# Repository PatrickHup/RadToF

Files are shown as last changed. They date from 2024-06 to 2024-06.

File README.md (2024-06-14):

<!--
*** Template source: https://github.com/othneildrew/Best-README-Template/blob/master/README.md
-->

<!-- PROJECT SHIELDS -->
<!--
*** I'm using markdown "reference style" links for readability.
*** Reference links are enclosed in brackets [ ] instead of parentheses ( ).
*** See the bottom of this document for the declaration of the reference variables
*** for contributors-url, forks-url, etc. This is an optional, concise syntax you may use.
*** https://www.markdownguide.org/basic-syntax/#reference-style-links
-->

<!-- PROJECT LOGO -->
<br />
<p align="center">
  <a>
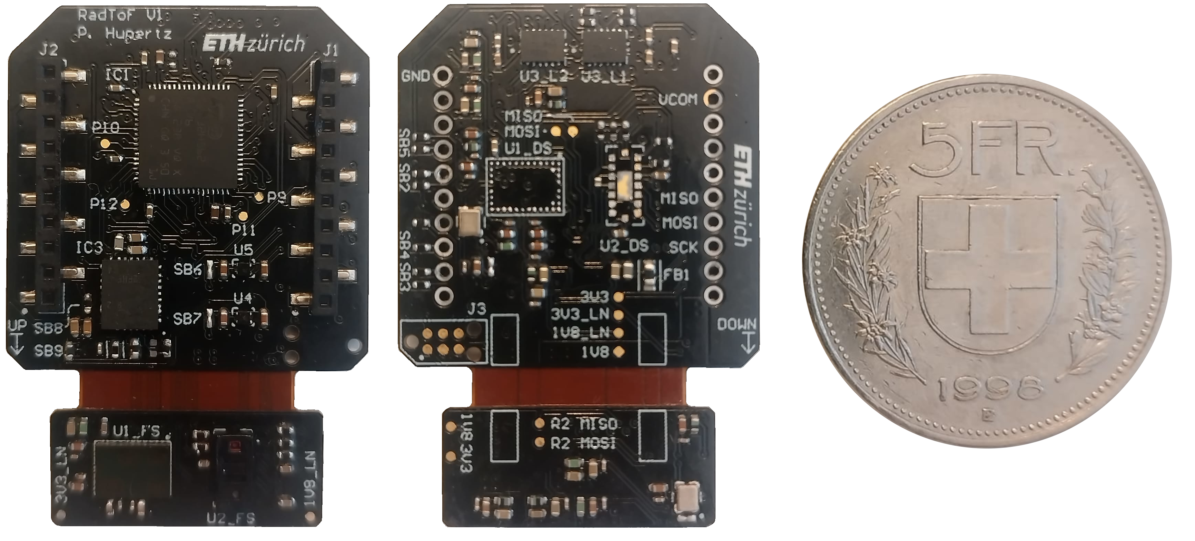
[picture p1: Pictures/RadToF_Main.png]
    
  </a>

  <h3 align="center">"RadToF" Radar/ToF Deck</h3>

  <p align="center">
    60 GHz radar extension board for the CrazyFlie 2.1
    <br />
    <a href="https://github.com/PatrickHup/Test"><strong>Explore the docs »</strong></a>
  </p>
</p>

<!-- TABLE OF CONTENTS -->
## Table of Contents

* [About the Project](#about-the-project)
* [Hardware](#hardware)
  * [Components](#hardware)
  * [PCB](#pcb)
* [Firmware](#firmware)
  * [Getting started](#getting-started)
* [Related work](#related-work)
* [Acknowledgment](#acknowledgment)

<!-- ABOUT THE PROJECT -->
## About The Project

The RadToF project aims to develop a Printed Circuit Board (PCB) optimized for drones, with a key focus on implementing the 60 GHz radar by Infineon Technologies. The goal is to enable drones to navigate more effectively and efficiently, driven by the increasing importance of autonomous nano drones across various sectors where sophisticated perception systems are crucial for safety and operational efficiency. By equipping drones with a radar system that delivers precise and reliable data, collision risks can be minimized, and operational autonomy can be improved.

**WARNING: USE AT YOUR OWN RISK, THERE MAY BE BUGS IN BOTH SOFTWARE AND HARDWARE**

## Hardware

The PCB accommodates four sensors: a radar and a depth camera pointing forwards, and the same setup pointing downwards. This board also includes an MCU that processes data before sending it to the CrazyFlie. The final board measures 3 cm x 4 cm and weighs 3.15 g.

### Components
The main sensor is the 60 GHz radar by Infineon Technologies, using FMCW (Frequency Modulated Continuous Wave) operations to measure distances. The radar features a compact design with a built-in transmitter and three receivers. Additionally, we utilize an 8x8 zone ranging sensor by STMicroelectronics. The MCU chosen for this project is the STM32H562RIV6, selected for its performance and small form factor.

An important aspect of the board is its power supply. The radar requires ultra-low noise 1V8 and 3V3, achieved using the "Ultra low-noise low ripple" power supply by Texas Instruments.

Main components:

* [BGT60TR13C][BGT60TR13C_url],			  60 GHz radar
* [VL53L8CX][VL53L8CX_url],     		  ToF multizone ranging sensor
* [STM32H562RIV6][STM32H562RIV6_url],		  Microcontroller
* [TPSM82912RDUR][TPSM82912RDUR_url],		  Ultra low noise switching regulator

Additional components:

* [TPS7A2018PDQNR][TPS7A2018PDQNR_url], 	  Ultra low noise LDO
* [SN74AXC4T774BQB][SN74AXC4T774BQB_url],	  Level shifter

### PCB 
The RadToF printed circuit board (PCB) is fabricated on a 4-layer Flex-Rigid PCB with a rigid PCB thickness of 0.84mm and a flex thickness of 0.16mm. Further information about the PCB can be found here:

File                                  | Content
--------------------------------------|--------
[RadToF.pdf]                          | Schematics of the deck.  
[RadToF_PDF3D.pdf]                    | Layout 3D view with details of components and nets.
[RadToF_BOM.xlsx]		      | Bill of material for the Deck PCB.
[RadToF_Draftsman.pdf]   	      | Draftsman of the PCB.
[RadToF.xls]		              | Layer stack of the Flex PCB.

The Altium project file [RadToF.prjpch] can be opened and edited using Altium Designer version 24.3.1

Top and bottom view of the board:

<p align="center">
	<a>
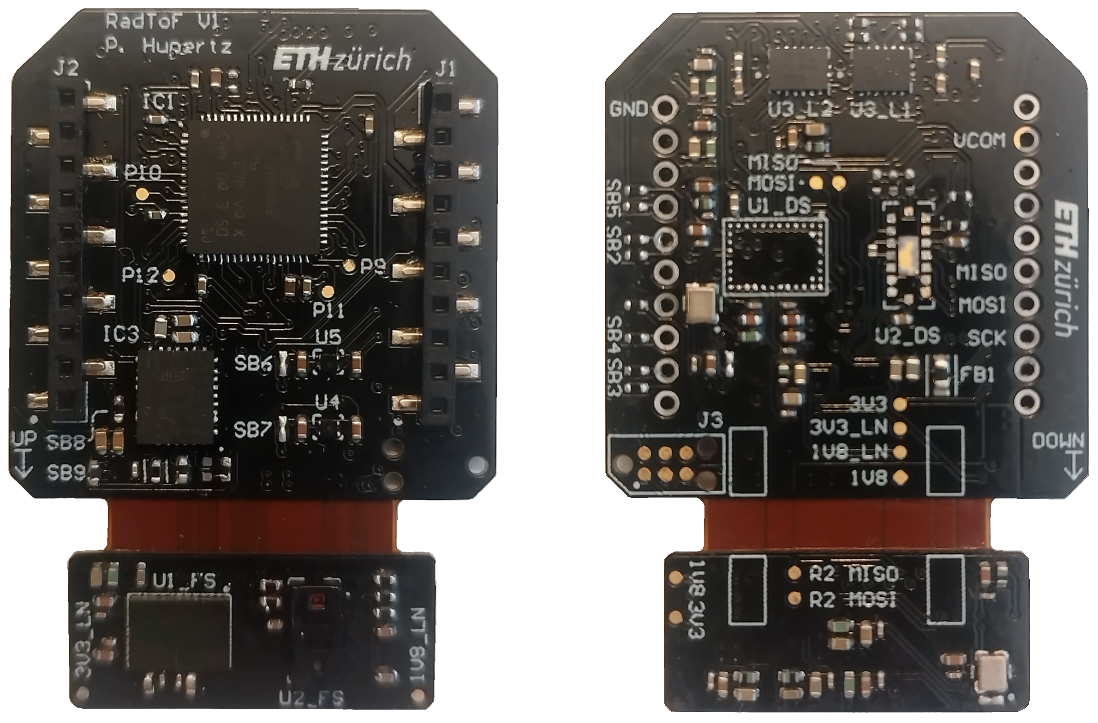
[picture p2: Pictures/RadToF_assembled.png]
	    
	</a>
</p>

#### Solder instruction:

#### Top side:

1. Pre-heat the PCB over 2-3 hours from room temperature to 250 °C to allow water molecules in the flex PCB to evaporate. This prevents delamination.
2. Apply 217 °C solder paste on the side marked "Top" with the help of a stencil if available. NOTE: do not apply solder paste on sensor pads.
3. Place components. Except for the sensors (radar and ToF).
5. Place the assembled board, "Top" side up, on pre preheated (250 °C) hot plate.
6. Wait for the solder paste to melt and remove to cool.
7. Verify the functionality of the power supply by checking voltages on debug pads.

#### Bottom side:

1. Apply 217 °C solder paste on the side marked "Bottom" with the help of a stencil if available. NOTE: do not apply solder paste on sensor pads.
2. Place components. Except for the sensors (radar and ToF).
3. Place the assembled board, "Bottom" side up, on pre preheated (150 °C) hot plate.
4. Use a hot air gun, set to 395 °C, to carefully melt the solder paste.
5. Verify the functionality of the MCU by trying to program it.

#### Radar soldering:

1. Do not apply solder paste
2. Place on 150 °C pre-heated hot plate
3. Heat with a heat gun set to 395 °C untill soldered

NOTE: if radar soldered unevenly, remove solder paste on pads and radar then re-ball radar with stencil

#### ToF sensor soldering:

WARNING: high temperature might damage ToF sensors plastic housing

1. Apply 138 °C solder paste on pads
2. Place on pre-heated hot plate at 150 °C
3. Carefully apply heat with a hot air gun

## Firmware

Needed software:

* [STM32cubeIDE][stm32cubeide_url], 		STM32 programmer and compiler version 1.15.1

The current state of the firmware is to be able to verify if the board is functional or not. The driver of the radar was provided by Tim Distel and the driver of the ToF can be found here: [ToF driver][ToF_driver_url].

### Getting started:

#### Material:

1. CrazyFlie 2.1
2. RadToF expansion deck
3. laptop
4. ST-LINK

#### How to program extension board:

1. Download STM32cubeIDE and the [Firmware] folder
2. open [.project] file with STM32cubeIDE (version 1.15.1)
3. Connect the extension board with a computer with ST-LINK
4. Compilie and upload firmware

## Related work

If you are interested in this work, you might also be interested in these:

1. [ToF deck][ToF_deck_url] offers a different approach for the extension board, featuring a ToF sensor facing forwards and backward.
2. [Quad deck][quad_deck_url] offers four ToF sensors, facing in every direction.
3. [Flow deck V2][flow_deck_url] offers a ToF and optical flow sensor facing downwards.

## Acknowledgment

Thanks go to:

Professor: Prof. Dr. Luca Benini

Supervisors: Dr. Tomasso Polonelli and Andrea Ronco

PCB experts: Hanna Müller and Alfonso Blanco

Additional help: Tim Distel and Luka Schultess

<!-- MARKDOWN LINKS & IMAGES -->
<!-- https://www.markdownguide.org/basic-syntax/#reference-style-links -->

<!--Subsection Hardware-->
[VL53L8CX_url]:    			https://www.st.com/resource/en/datasheet/vl53l8cx.pdf
[crazyflie_url]:   			https://www.bitcraze.io/products/crazyflie-2-1/
[BGT60TR13C_url]:			https://www.infineon.com/dgdl/Infineon-DS_BGT60TR13C-DataSheet-v02_49-EN.pdf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
[STM32H562RIV6_url]:			https://www.st.com/resource/en/datasheet/stm32h562ag.pdf
[TPSM82912RDUR_url]:			https://www.ti.com/lit/ds/symlink/tpsm82913e.pdf
[TPS7A2018PDQNR_url]:			https://www.ti.com/lit/ds/symlink/tps7a20.pdf
[SN74AXC4T774BQB_url]:			https://www.ti.com/lit/ds/symlink/sn74axc4t774.pdf
[stm32cubeide_url]: 			https://www.st.com/en/development-tools/stm32cubeide.html

[ToF_driver_url]: 			https://www.st.com/en/embedded-software/stsw-img040.html
[ToF_deck_url]: 			https://github.com/ETH-PBL/Matrix_ToF_Drones
[quad_deck_url]:			https://github.com/ETH-PBL/NanoSLAM
[flow_deck_url]:			https://www.bitcraze.io/products/flow-deck-v2/
<!--Subsection PCB-->
[RadToF.pdf]:                          /Hardware/Project_Output/RadToF.pdf
[RadToF_PDF3D.pdf]:                    /Hardware/Project_Output/RadToF_PDF3D.pdf
[RadToF_BOM.xlsx]:                     /Hardware/Project_Output/RadToF_BOM.xlsx
[RadToF_Draftsman.pdf]:                /Hardware/Project_Output/RadToF_Draftsman.pdf
[RadToF.xls]:                          /Hardware/Project_Output/RadToF.xls
[RadToF.prjpch]:                       /Hardware/RadToF.PrjPcb
[.project]:			       /Firmware/.project
[Firmware]:			       /Firmware

[stmcubeIDE_url]:	               https://www.st.com/en/development-tools/stm32cubeide.html
[altium_url]:	                       https://www.altium.com/

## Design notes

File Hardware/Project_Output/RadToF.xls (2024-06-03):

Board Stack Report
Stack Up |  |  | Layer Stack
Layer | Full stack | Flex stack | Name | Material | Thickness | Constant
1 |  |  | Top Overlay |  | 0mil
2 |  |  | Flex stack Top Coverlay | FC-001 | 1.476mil | 4
3 |  |  | Top Solder | Solder Resist | 0.8mil | 3.5
4 |  |  | Top Layer |  | 1.4mil
5 |  |  | Dielectric 4 | FR4 HTG | 9.8mil | 4.1
6 |  |  | Dielectric 2 | 1080 | 2.8mil | 4.1
7 |  |  | Layer 1 | CF-004 | 0.7mil
8 |  |  | Dielectric 1 | Polyimide | 2mil | 4.8
9 |  |  | Layer 2 | CF-004 | 0.7mil
10 |  |  | Dielectric 5 | 1080 | 2.8mil | 4.1
11 |  |  | Dielectric 3 | FR4 HTG | 9.8mil | 4.1
12 |  |  | Bottom Layer |  | 1.4mil
13 |  |  | Bottom Solder | Solder Resist | 0.8mil | 3.5
14 |  |  | Flex stack Bottom Coverlay | FC-001 | 1.476mil | 4
15 |  |  | Bottom Overlay |  | 0mil
 | Height : 33mil | Height : 6.353mil

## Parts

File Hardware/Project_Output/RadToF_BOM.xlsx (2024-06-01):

Line # | Name | Description | Designator | Revision ID | Revision State | Revision Status | Quantity | Manufacturer 1 | Manufacturer Part Number 1 | Manufacturer Lifecycle 1 | Supplier 1 | Supplier Part Number 1 | Supplier Unit Price 1 | Supplier Subtotal 1
 | Capacitor 100nF +/-20% 50V 0402 | Chip Capacitor, 100nF +/-20%, 50V, 0402, Thickness 0.6 mm | C1_DS, C1_FS, C2_DS, C2_FS, C14, C16_DS, C16_FS, C31, C33, C34, C35, C37, C38, C39, C40, C41, C42 |  | Unknown server |  | 17 | Murata | GRM155R71H104KE14D | Volume Production | Mouser | 81-GRM155R71H104KE4D | 0.01371 | 0.23314
 | C_GRM035R60J475ME15D | CAP CER 4.7uF 6.3V X5R 0201 | C5_DS, C5_FS |  | Unknown server |  | 2 | Murata | GRM035R60J475ME15D | Volume Production | Digikey | 490-13230-1-ND | 0.21943 | 0.43885
 | C_GRM155R61A106ME11D | CAP CER 10uF 10V X5R 20% 0402 | C6_DS, C6_FS, C9_DS, C9_FS, C10_DS, C10_FS, C17_DS, C17_FS, C19_DS, C19_FS, C52, C53 |  | Unknown server |  | 12 | Murata | GRM155R71H103KA88D | Volume Production | Mouser | 81-GRM155R71H103KA8D | 0.01189 | 0.14263
 | C_GRM155R61E105KA12J | CAP CER 1uF 25V X5R 0402 | C7_DS, C7_FS, C12_DS, C12_FS, C20_DS, C20_FS, C22_DS, C22_FS, C24_DS, C24_FS, C26_DS, C26_FS, C28_DS, C28_FS, C42_OSC_D, C42_OSC_F, C56, C57, C58, C59 |  | Unknown server |  | 20 | Murata | GRM155R61E105KA12J | Volume Production | Farnell | 3790417 | 0.01419 | 0.28388
 | C_GRM033R70J103JA01D | CAP CER 10nF 6.3V X7R 0201 | C8_DS, C8_FS, C11_DS, C11_FS, C13_DS, C13_FS, C18_DS, C18_FS, C21_DS, C21_FS, C23_DS, C23_FS, C25_DS, C25_FS, C27_DS, C27_FS, C29_DS, C29_FS, C43_OSC_D, C43_OSC_F |  | Unknown server |  | 20 | Murata | GRM033R70J103JA01D | Volume Production | Mouser | 81-GRM033R70J103JA1D | 0.00823 | 0.16457
 | Capacitor 2,2µF +/-20% 10V 0402 | Chip Capacitor, 2,2µF +/-20%, 10V, 0402, Thickness 0.6 mm | C15, C32 |  | Unknown server |  | 2 | Murata | GRM155R61C225KE11D | Volume Production | Arrow Electronics | GRM155R61C225KE11D | 0.14208 | 0.28416
 | C_GRM155R71H152JA01D | CAP CER 1.5nF 50V X7R 0402 | C30_DS, C30_FS |  | Unknown server |  | 2 | Murata | GRM155R71H103KA88D | Volume Production | Mouser | 81-GRM155R71H103KA8D | 0.01189 | 0.11886
 | C_GRM158R60J226ME01D | CAP CER 22uF 6.3V X5R 0402 | C47, C48, C49, C50, C51 |  | Unknown server |  | 5 | Murata | GRM155R71H103KA88D | Volume Production | Mouser | 81-GRM155R71H103KA8D | 0.01189 | 0.11886
 | C_GRT033C80J224KE01D | CAP CER 0.22uF 6.3V X6S 0201 | C55 |  | Unknown server |  | 1 | Murata | GRT033C80J224KE01D | Volume Production | Arrow Electronics | GRT033C80J224KE01D | 0.0832 | 0.0832
 | BLE18PS080SN1D | Ferrite Chip Bead 8A 8.5Ohm 2-Pin 0603 Paper T/R | FB1 |  | Unknown server |  | 1 | Murata | BLE18PS080SN1D | Volume Production | Digikey | 490-BLE18PS080SN1DCT-ND | 0.256 | 0.256
 | STM32H562RIV6 | ARM Microcontrollers - MCU Arm Cortex-M33 32-bit 250 MHz, up to 2 Mbytes of Flash, 640KB of RAM, I3C, DCMI | IC1 |  | Not managed |  | 1
 | TPSM82912RDUR | Switching Voltage Regulators 17-V, 2-A low-noise and low-ripple buck module with integrated ferrite bead filter compensation 28-B0QFN -40 to 125 | IC3 |  | Not managed |  | 1
 | Left | Header to connect to crazy flie pins | J1 |  | Not managed |  | 1
 | Right | Header to connect to crazy flie pins | J2 |  | Not managed |  | 1
 | TC2030-MCP-NL | CABLE TAG-CONNECT IN-CIRCUIT | J3 |  | Not managed |  | 1
 | L_LQG15WZ4N7B02D | IND 4.7nH 800mA 110 mOHM 0402 | L1_DS, L1_FS, L2_DS, L2_FS, L3_DS, L3_FS, L4_DS, L4_FS, L5_DS, L5_FS, L6_DS, L6_FS |  | Unknown server |  | 12 | Murata | LQG15WZ4N7B02D | Volume Production | Mouser | 81-LQG15WZ4N7B02D | 0.13988 | 1.68
 | Test Pad |  | P1_DS, P1_FS, P2_DS, P2_FS, P3_DS, P3_FS, P4_DS, P4_FS |  | Not managed |  | 8
 |  |  | P5, P6, P7, P8, P9, P10, P11, P12 |  | Not managed |  | 8
 | Resistor 47K5 +/-1 % 0402 63 mW | Chip Resistor, 47,5 kOhms, +/-1 %, 63 mW, -55 to 155 degC, 0402 | R1_DS, R1_FS, R2_DS, R2_FS, R3_DS, R3_FS, R4_DS, R4_FS, R5_DS, R5_FS, R6 |  | Unknown server |  | 11 | Vishay | CRCW040247K5FKED | Volume Production | Newark | 52K7100 | 0.00457 | 0.05029
 | Resistor 10K +/-1 % 0402 63 mW | Chip Resistor, 10 kOhms, +/-1 %, 63 mW, -55 to 125 degC, 0402 | R7 |  | Unknown server |  | 1 | Panasonic | ERJ-2RKF1002X | Volume Production | Digikey | P10.0KLCT-ND | 0.09143 | 0.09143
 | 301KR2F | 301K 0.063W 1% 0402 (1005 Metric) SMD | R8, R9, R10, R13, R17, R18, R23, R24 |  | Unknown server |  | 8
 | 4.87k | Automotive Metal Thin Film Chip Resistor, 0402, 4.87kΩ, 0.1%, 25ppm/°C, 0.0625W, 75V | R11 |  | Unknown server |  | 1 | Susumu | RG1005P-4871-B-T5 | Volume Production | Mouser | 754-RG1005P-4871-BT5 | 0.24685 | 0.24685
 | Resistor 15k +/-1% 0402 63 mW | Chip Resistor, 15 KOhm, +/- 1%, 0.063 W, -55 to 155 degC, 0402 (1005 Metric) | R12 |  | Unknown server |  | 1 | Yageo | RC0402FR-0715KL | Volume Production | Rs | 6186009 | 0.00177 | 0.00177
 | Jumper 0402 | Jumper 0402 | R14, R15 |  | Unknown server |  | 2 | Yageo | RC0402JR-070RL | Volume Production | Rs | 6185804 | 0.00086 | 0.00172
 | SB2_0402_close | Custom Solder jumper, closed | SB1_OSC_D, SB1_OSC_F, SB6, SB7 |  | Not managed |  | 4
 | SB2_0402 | Custom Solder jumper, open | SB2, SB3, SB4, SB5, SB8, SB9 |  | Not managed |  | 6
 | BGT60TR13D | XENSIV 60 GHz radar system platform | U1_DS, U1_FS |  | Not managed |  | 2
 | VL53L8CXV0GC | Low-power high-performance 8x8 multizone Time-of-Flight sensor 940 nm, 6.4x3.0x1.75 mm, -30 to 85C | U2_DS, U2_FS |  | Not managed |  | 2
 | SN74AXC4T774BQB | 4-Bit Dual-Supply Bus Transceiver with Independent Direction Control, Configurable Voltage Translation, and Tri-State Outputs | U3_L1, U3_L2 |  | Not managed |  | 2 | Texas Instruments | SN74AXC4T774BQBR | Volume Production | Mouser | 595-SN74AXC4T774BQBR | 0.84113 | 1.68
 | TPS7A2018PDQNR | 1.8V 300-mA ultra-low-noise low-IQ low-dropout (LDO) linear regulator with high PSRR | U4, U5 |  | Not managed |  | 2 | Texas Instruments | TPS7A2018PDQNR | Volume Production | Mouser | 595-TPS7A2018PDQNR | 0.42057 | 0.84113
 | KC2016Z40.0000C1KX00 | Standard Clock Oscillators 40 Mhz 20 Ppm 15 Pf Cmos Aec-Q200 | Y1_OSC_D, Y1_OSC_F |  | Not managed |  | 2 | Kyocera AVX | KC2016Z40.0000C1KX00 |  | Digikey | 478-KC2016Z40.0000C1KX00CT-ND | 1.11 | 2.21

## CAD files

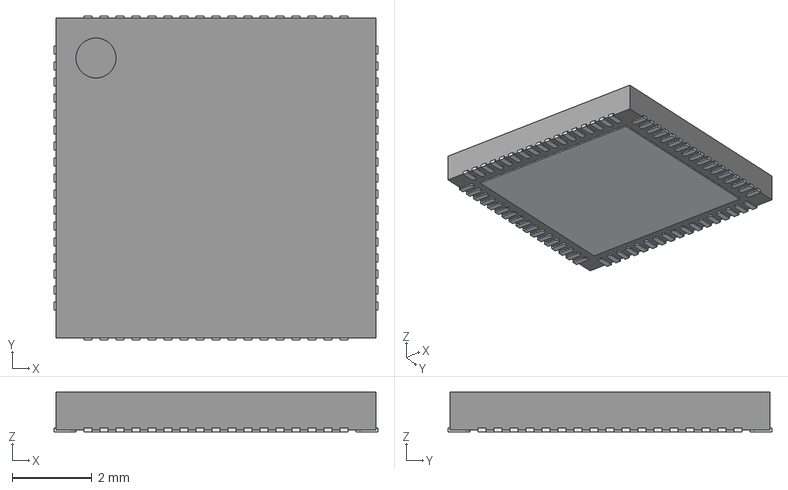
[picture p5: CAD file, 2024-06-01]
Hardware/3D models/STM32H562RIV6.stp
8.10 x 8.10 x 1.00 mm
ThermalPin
PinsArrayLR
PinsArrayTB

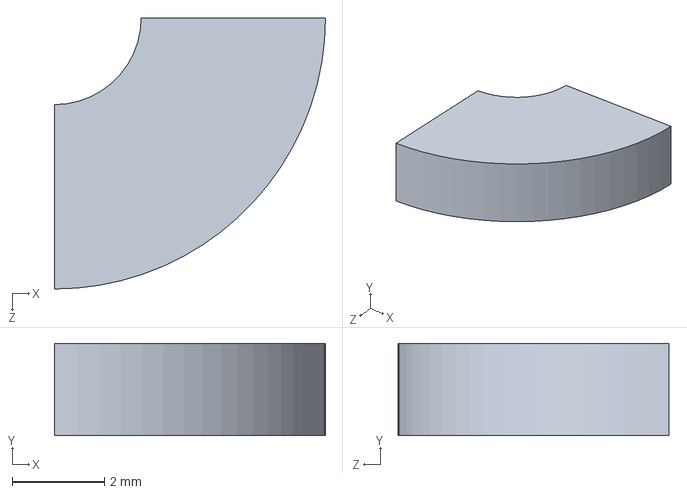
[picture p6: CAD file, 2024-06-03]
Hardware/Bracket/Bracket.SLDPRT
5.88 x 2.00 x 5.88 mm

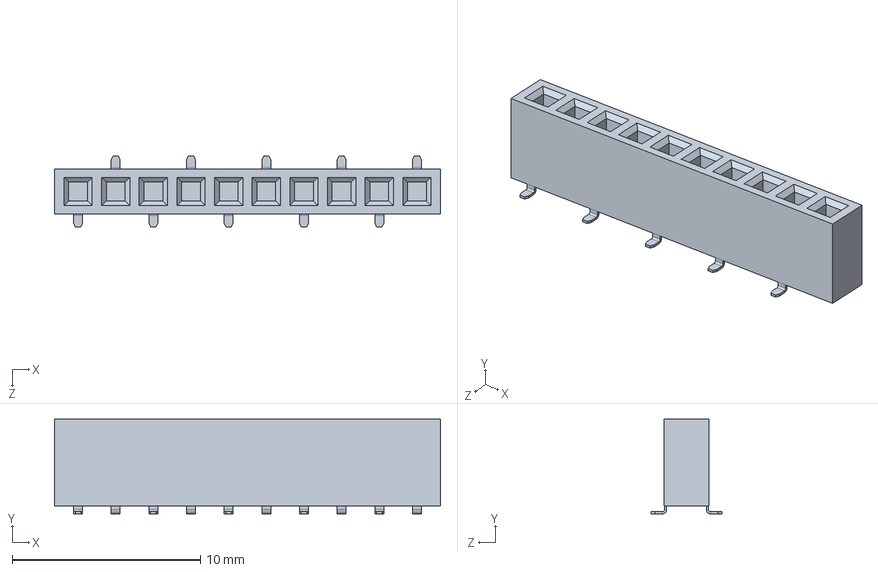
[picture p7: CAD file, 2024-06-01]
Hardware/3D models/1X10_2MM_SMD.SLDPRT
20.5 x 5.03 x 3.76 mm

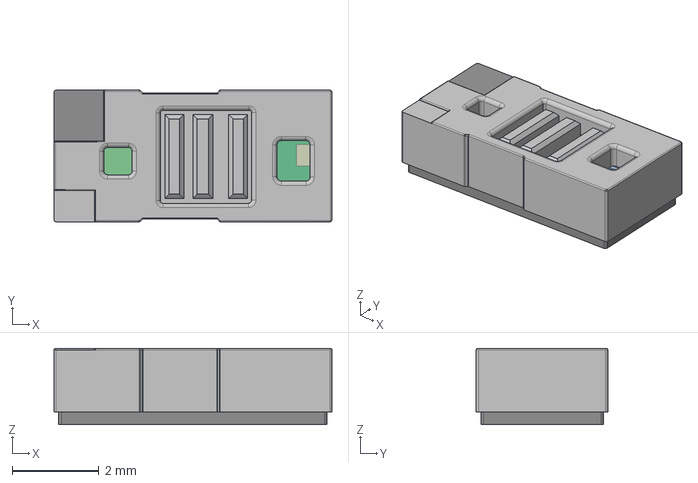
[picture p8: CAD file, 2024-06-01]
Hardware/3D models/VL53L8CXV0GC_1.stp
6.40 x 3.03 x 1.75 mm

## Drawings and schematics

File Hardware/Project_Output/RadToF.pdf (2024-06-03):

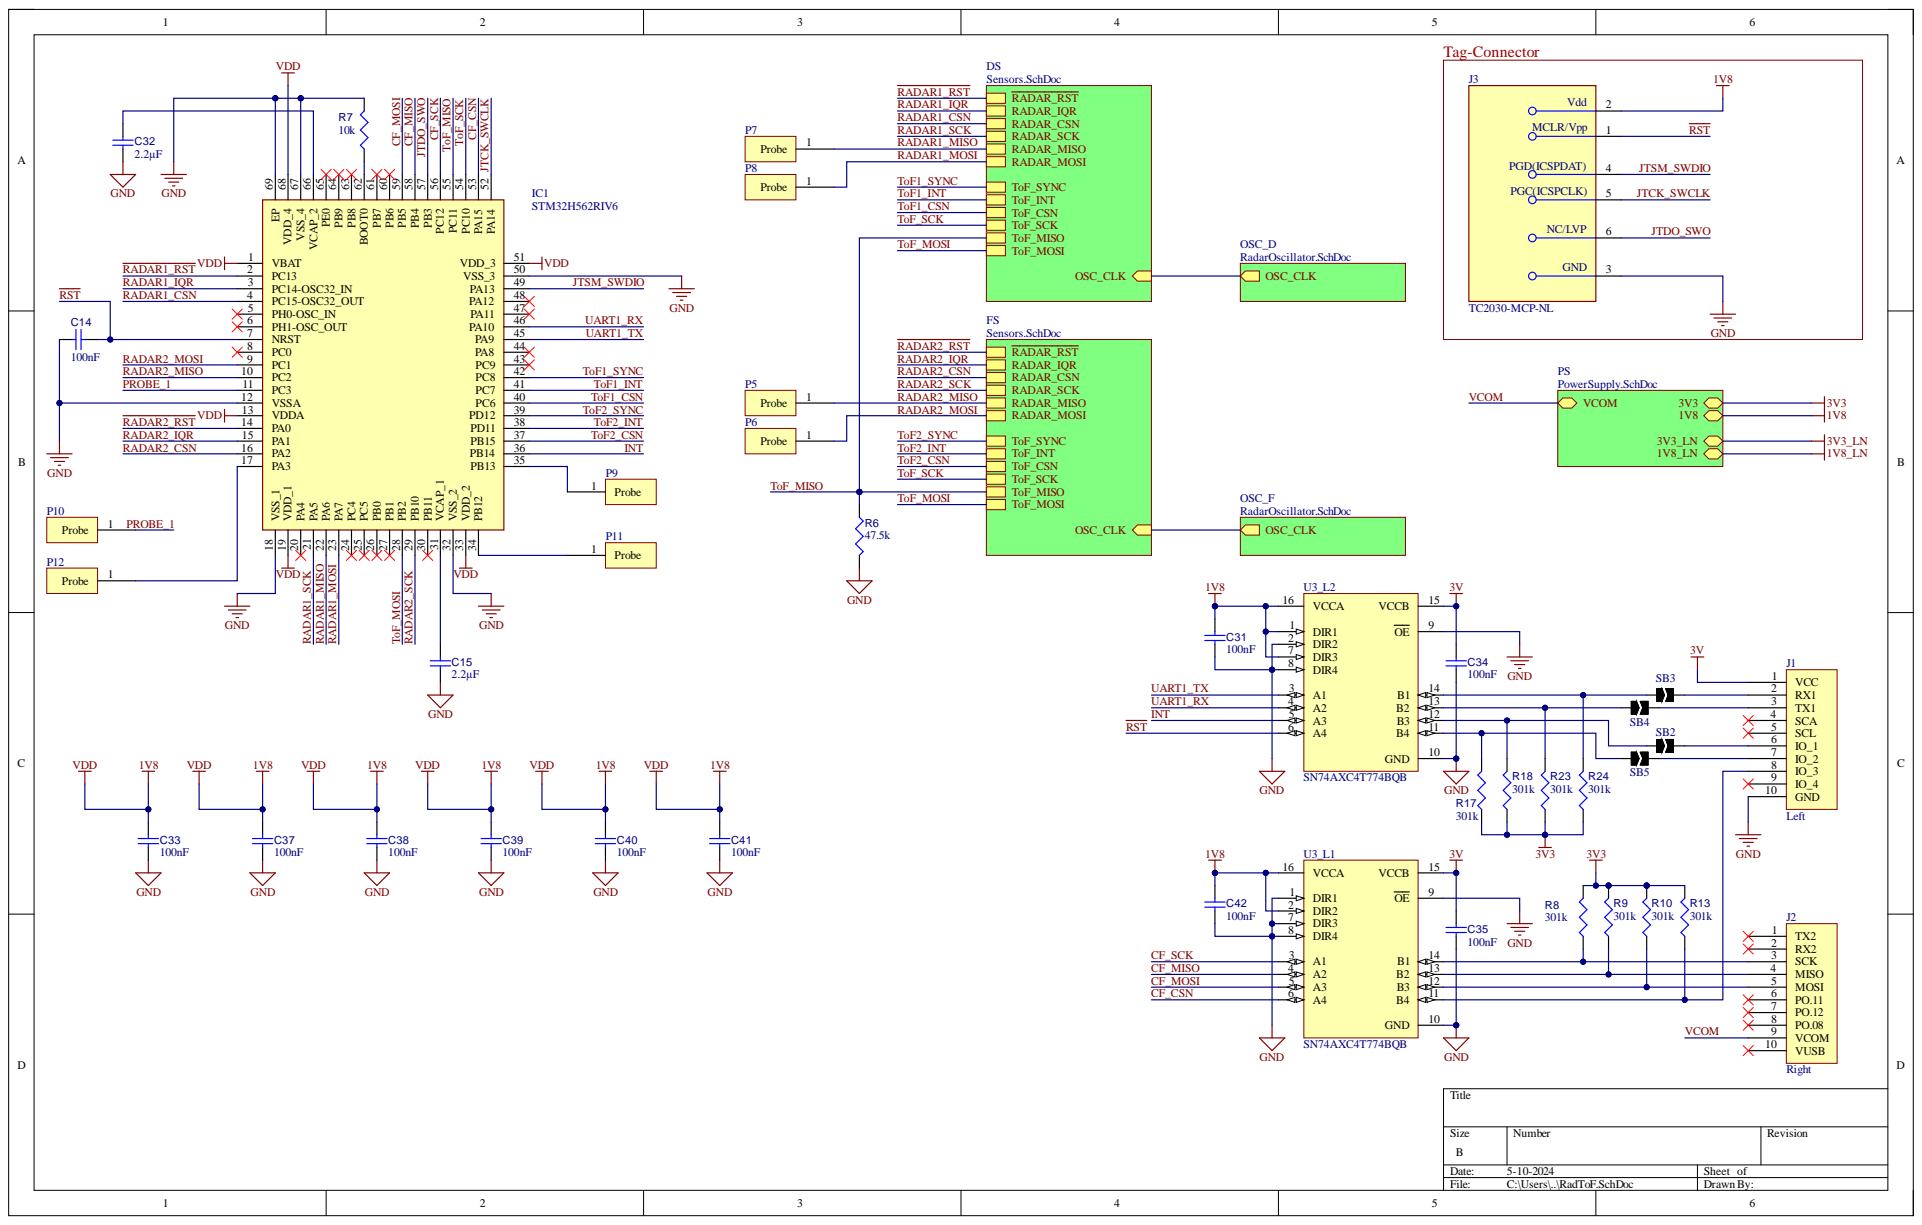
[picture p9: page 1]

Si z e | Num b er | Revi s i on

e : 5-10-20 24 | Sheet of
Fi l e : C : \U ser s \..\ RadToF.Sch Do c | D rawn By:

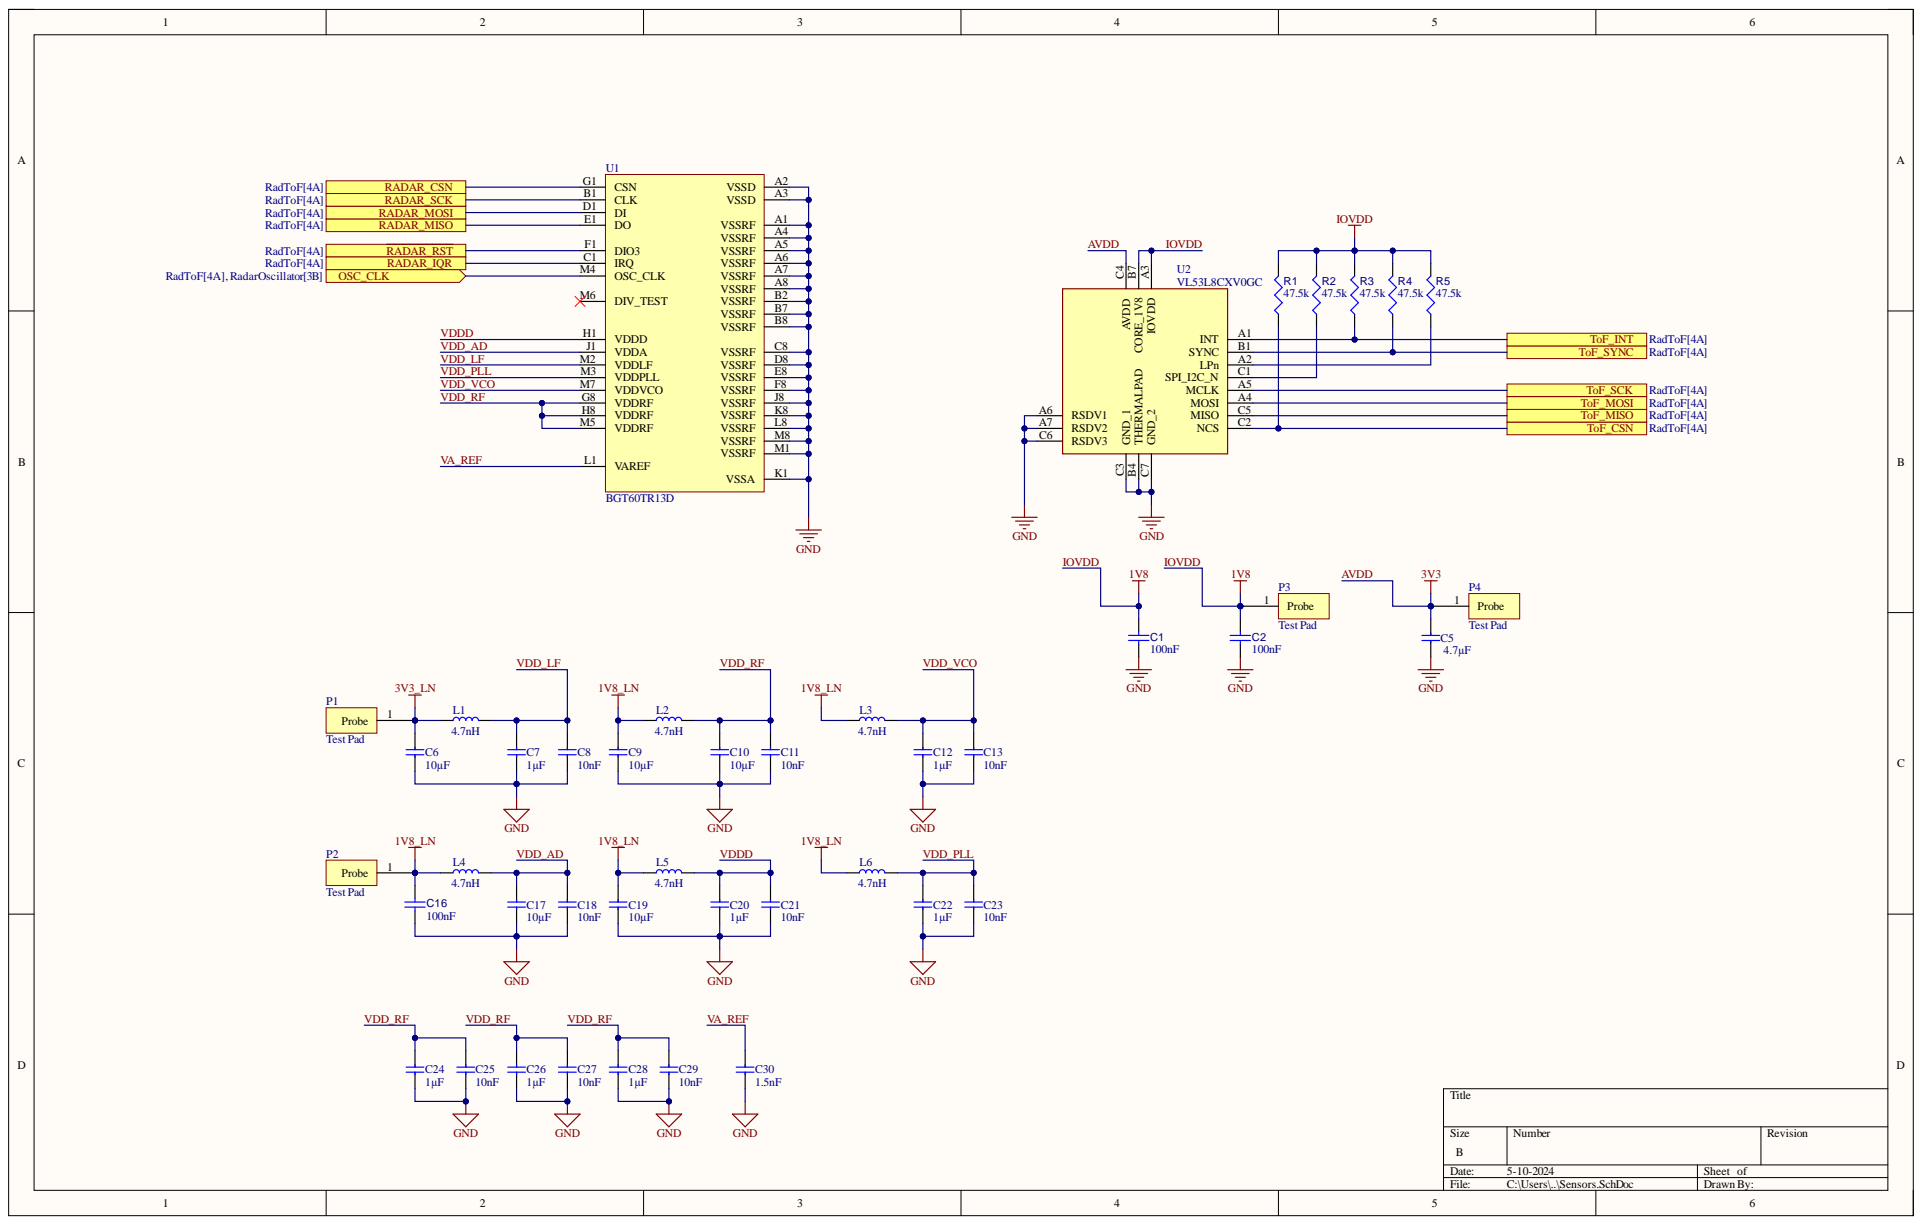
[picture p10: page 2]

Size B | Number | Revision

Date: 5-10-2024 | Sheet of
File: C:\Users\..\Sensors.SchDoc | Drawn By:

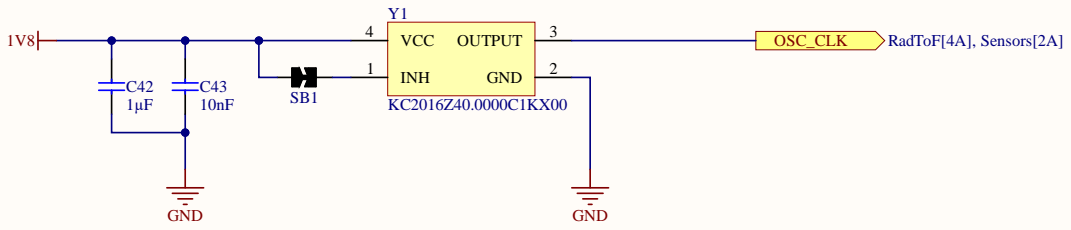
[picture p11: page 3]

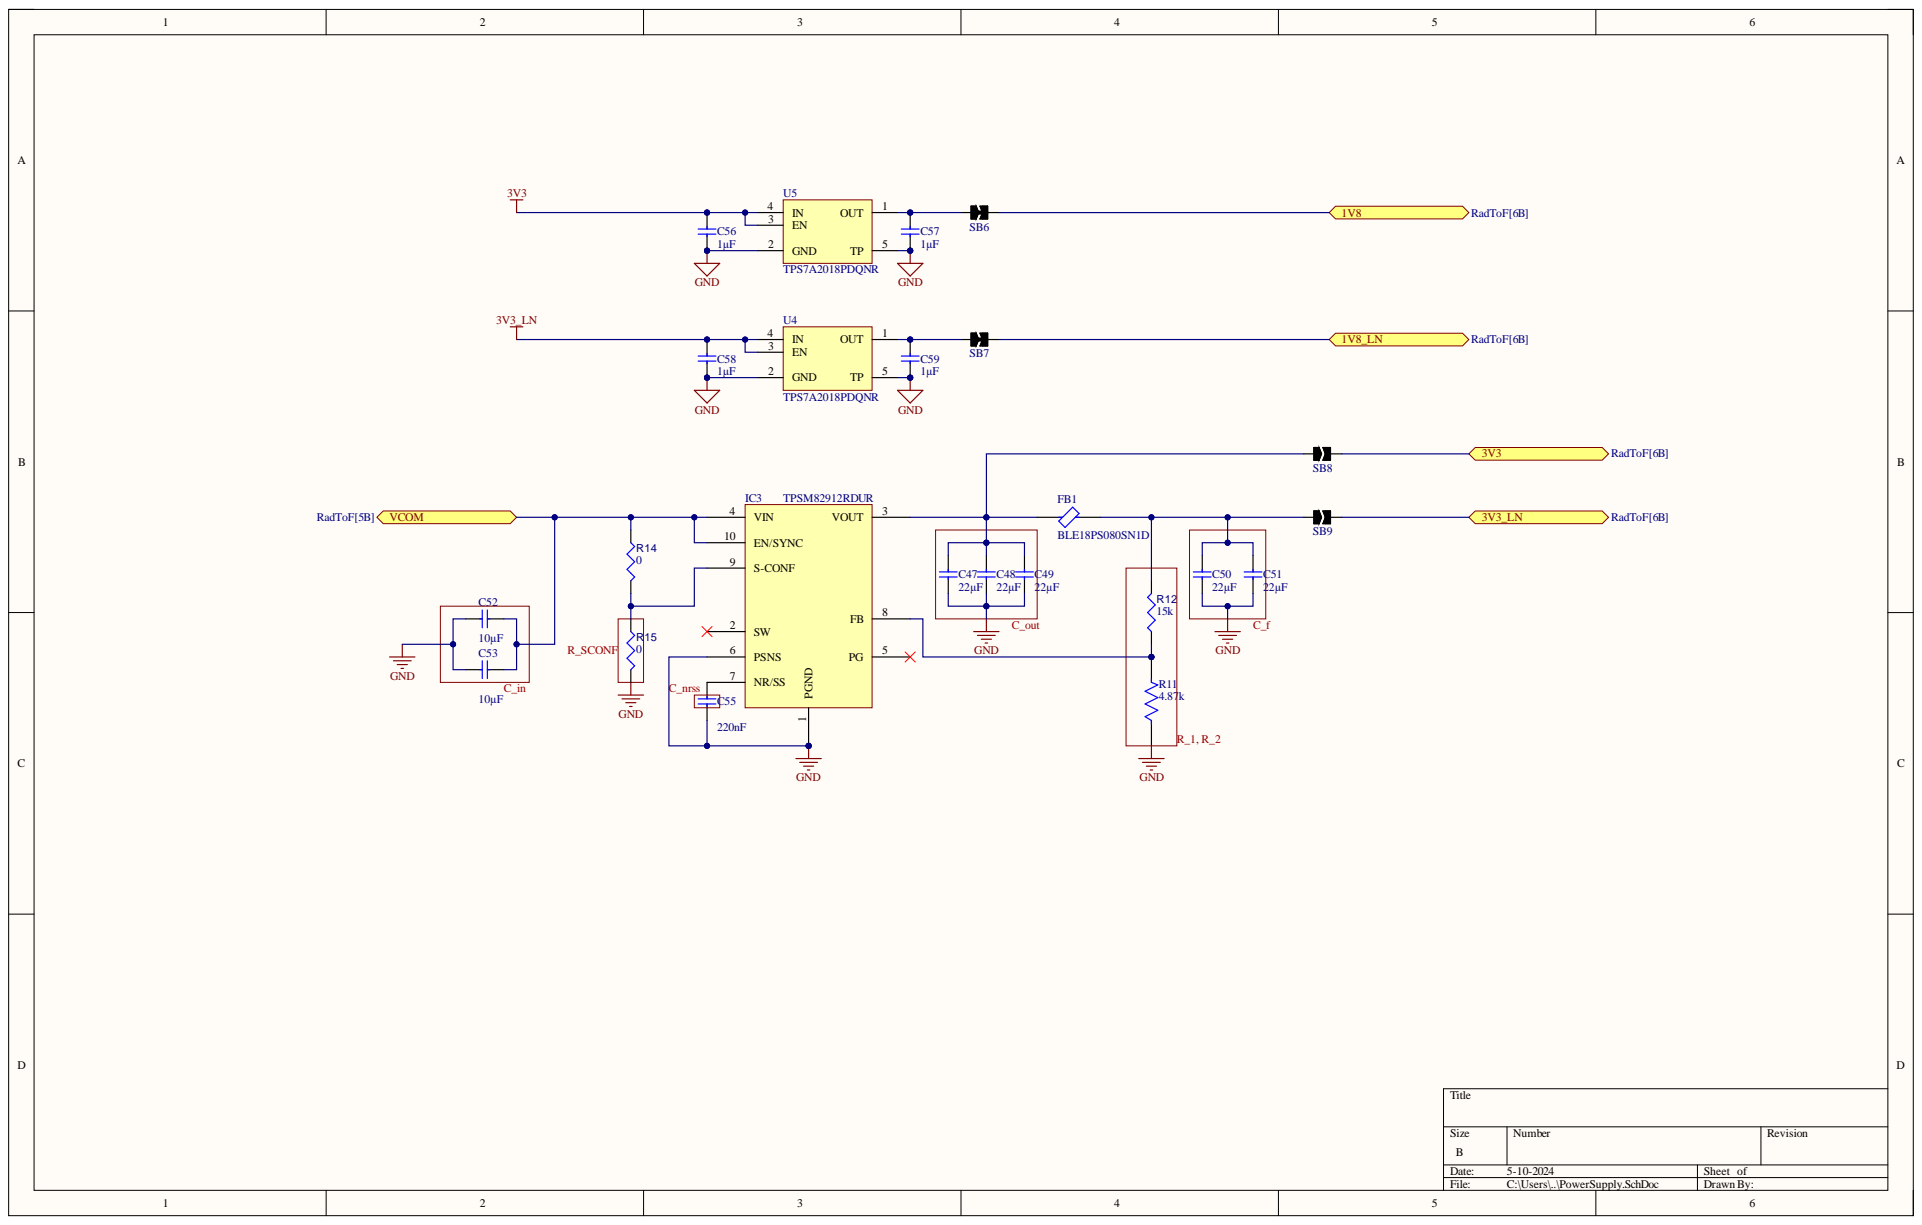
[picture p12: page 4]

Size B | Number | Revision

Date: 5-10-2024 | Sheet of
File: C:\Users\..\PowerSupply.SchDoc | Drawn By:

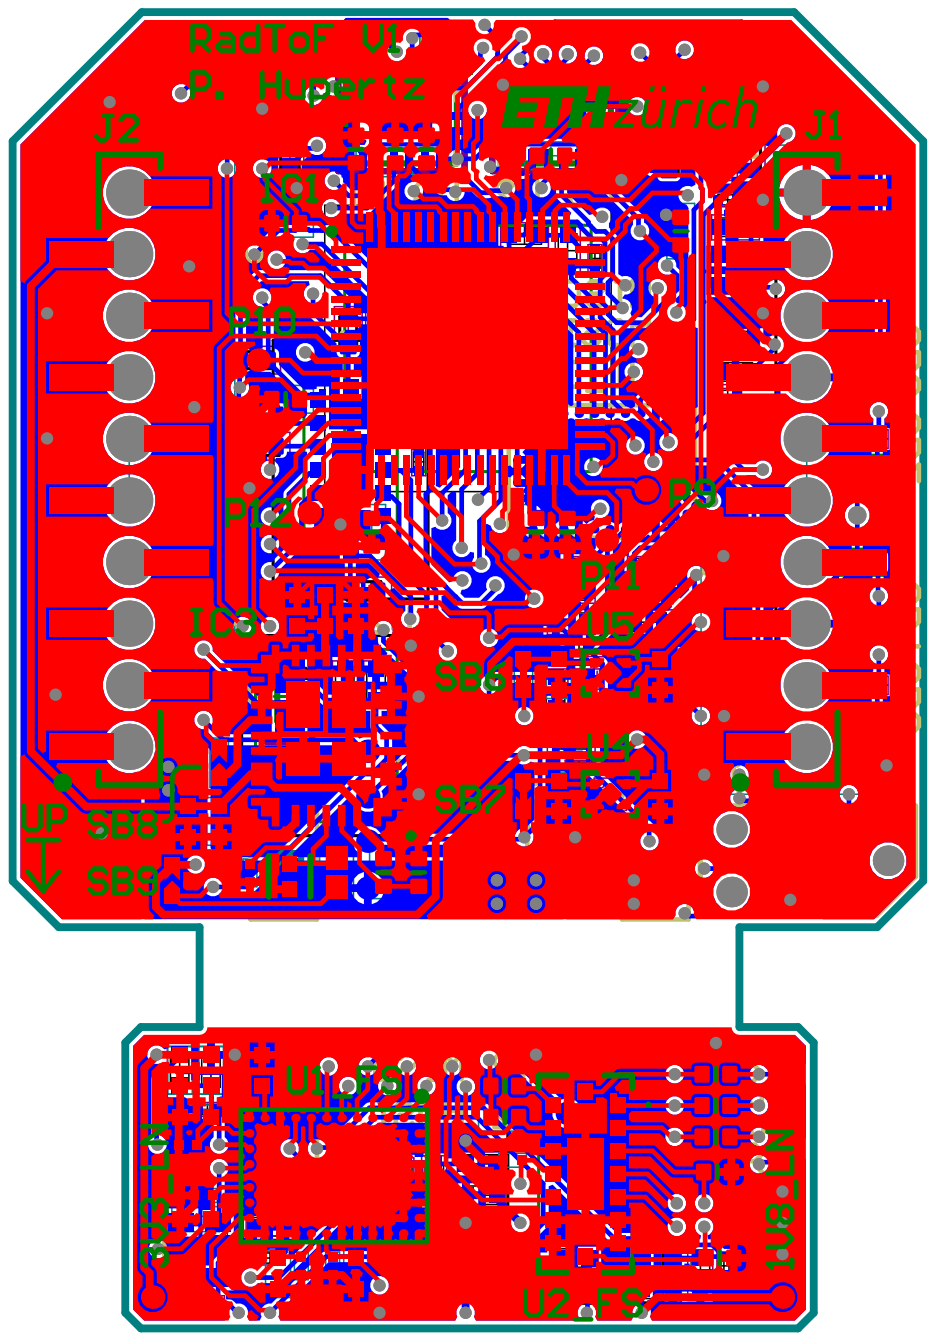
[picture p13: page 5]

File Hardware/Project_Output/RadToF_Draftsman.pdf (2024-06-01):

# Realistic Top and Bottom view

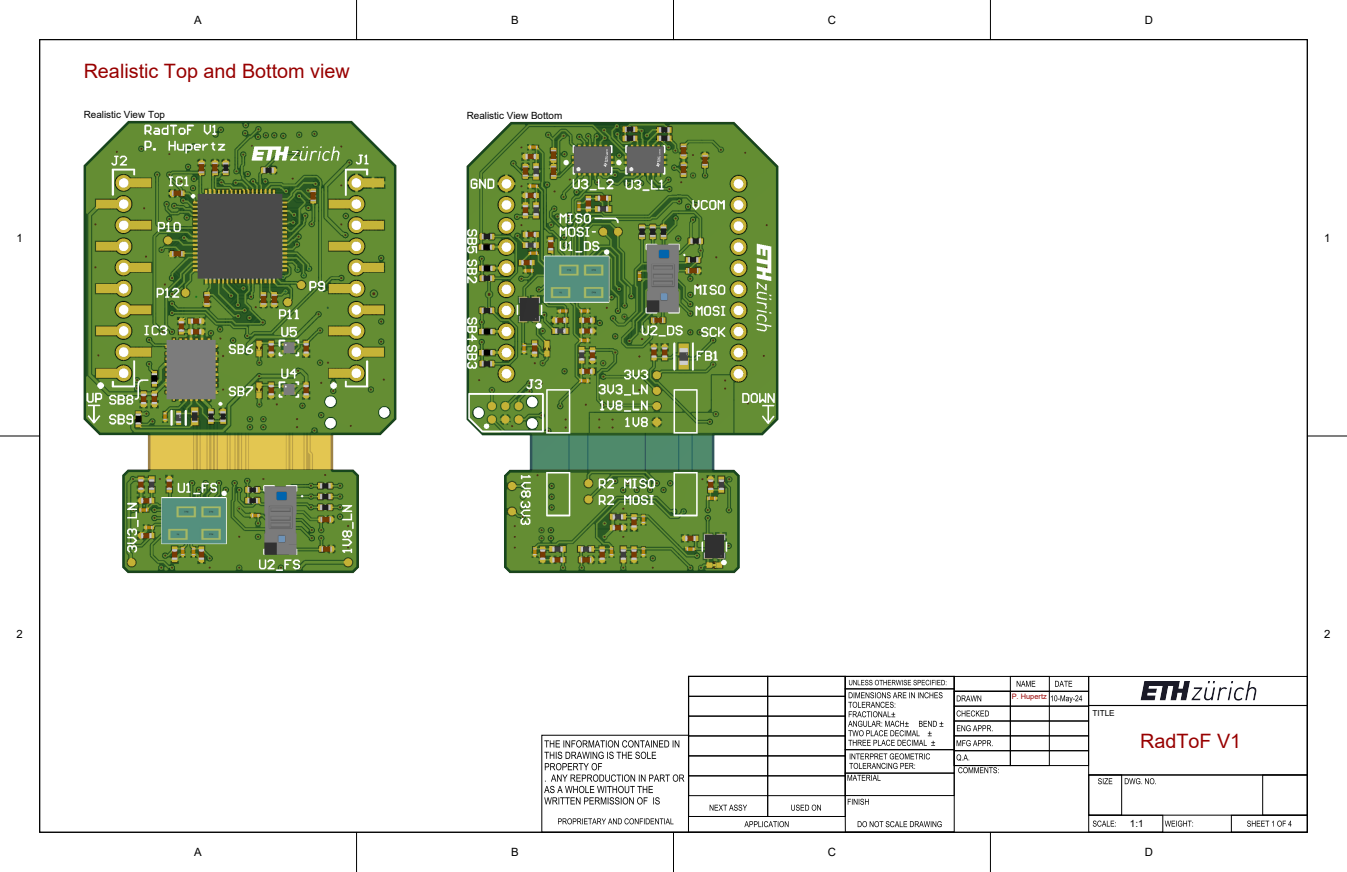
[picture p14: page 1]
TITLE; Realistic View Top; Realistic View Bottom; RadToF V1; P. Hupertz

# Rigid-Flex Layer stack

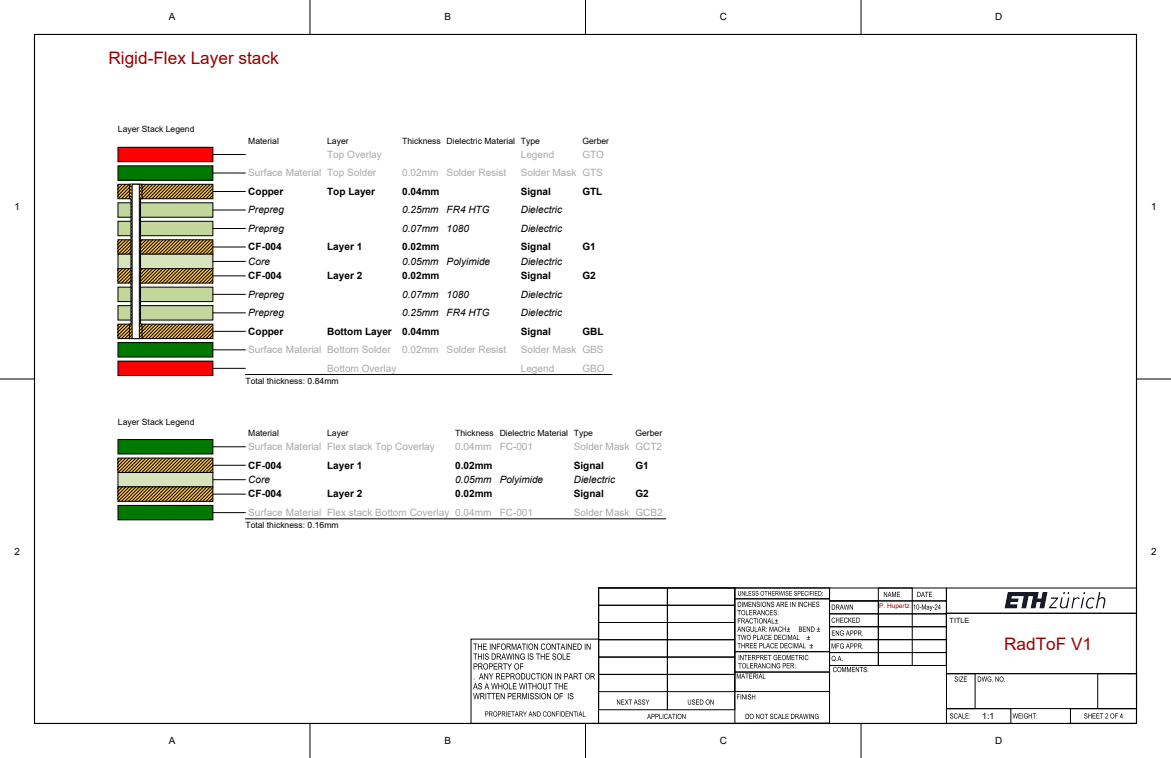
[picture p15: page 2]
TITLE; Material; Layer; Thickness Dielectric Material Type; Gerber; Top Overlay; Legend; GTO; Surface Material Top Solder; 0.02mm Solder Resist; Solder Mask GTS; Copper; Top Layer; Signal; GTL; Prepreg; 0.25mm FR4 HTG; Dielectric; Layer 1; Core; 0.05mm Polyimide; Layer 2; Bottom Layer 0.04mm; GBL; Surface Material Bottom Solder 0.02mm Solder Resist; Solder Mask GBS; Bottom Overlay; GBO; Total thickness: 0.84mm; Surface Material Flex stack Top Coverlay; Solder Mask GCT2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

Layer Stack Legend

# Layer print

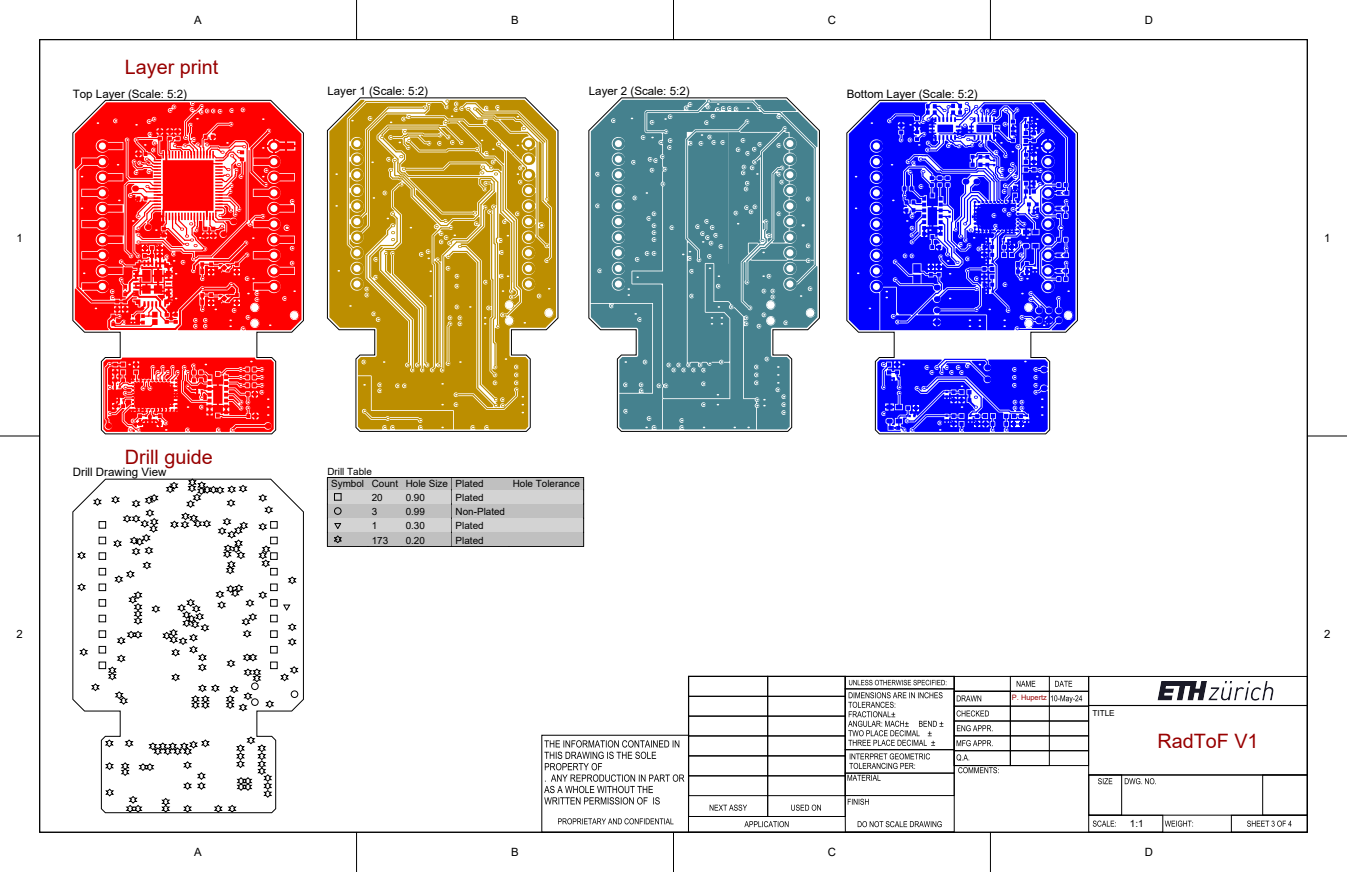
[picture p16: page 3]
Top Layer (Scale: 5:2); Layer 1 (Scale: 5:2); Layer 2 (Scale: 5:2); Bottom Layer (Scale: 5:2); TITLE; RadToF V1; Drill guide; Drill Table; P. Hupertz

Drill Drawing View

Symbol | Count | Hole Size | Plated | Hole Tolerance

20 | 0.90 | Plated
3 | 0.99 | Non-Plated
1 | 0.30 | Plated
173 | 0.20 | Plated

## C24_DSC²⁰_DS

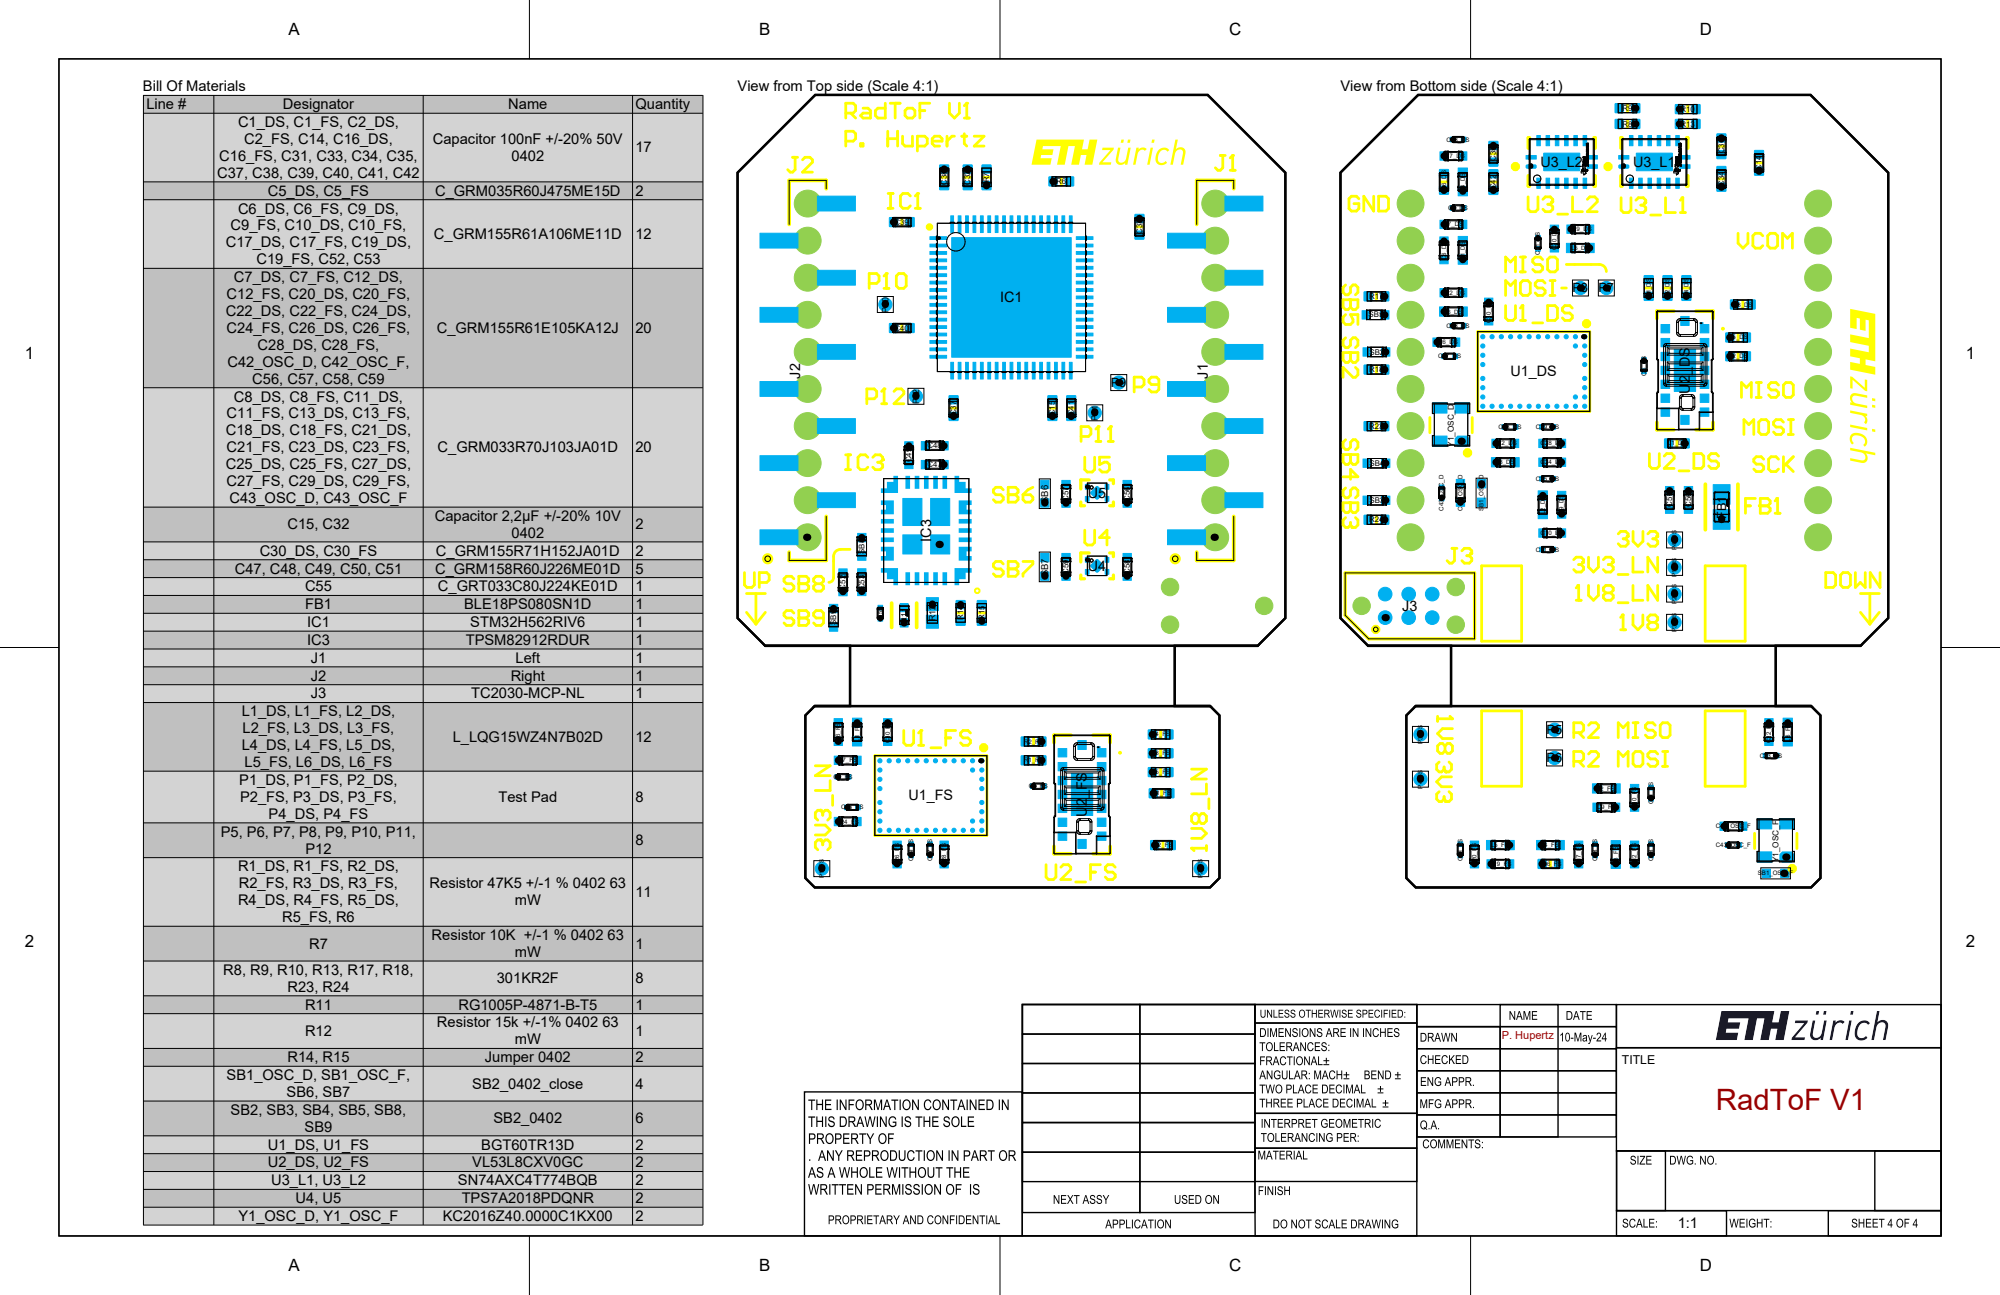
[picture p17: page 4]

View from Top side (Scale 4:1)

View from Bottom side (Scale 4:1)

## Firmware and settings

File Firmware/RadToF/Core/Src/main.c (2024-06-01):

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
/* Includes ------------------------------------------------------------------*/
#include "main.h"

/* USER CODE BEGIN Includes */
#include "bgt60utr13d.h"
#include "vl53l8cx_api.h"

/* USER CODE END Includes */

/* USER CODE BEGIN PD */
#define PRINT_ERRORS_ONLY 0

#define RAD_1_CS_PORT  GPIOC
#define RAD_1_CS_PIN   GPIO_PIN_15
#define RAD_1_RST_PORT GPIOC
#define RAD_1_RT_PIN   GPIO_PIN_13

#define RAD_2_CS_PORT  GPIOB
#define RAD_2_CS_PIN   GPIO_PIN_10
#define RAD_2_RST_PORT GPIOA
#define RAD_2_RT_PIN   GPIO_PIN_0

/* USER CODE END PD */


SPI_HandleTypeDef hspi1;
SPI_HandleTypeDef hspi2;
SPI_HandleTypeDef hspi3;
SPI_HandleTypeDef hspi6;

UART_HandleTypeDef huart1;

/* USER CODE BEGIN PV */
int status;
VL53L8CX_Configuration 	Dev;
uint8_t resolution, isAlive;
/* USER CODE END PV */

void SystemClock_Config(void);
static void MX_GPIO_Init(void);
static void MX_SPI1_Init(void);
static void MX_SPI2_Init(void);
static void MX_SPI3_Init(void);
static void MX_SPI6_Init(void);
static void MX_USART1_UART_Init(void);
/* USER CODE BEGIN 0 */

// Functions for handle struct
bgt60utr13d_err_t read_regs_1(const uint8_t *send_buf, uint32_t n, uint8_t *buf)
{
  //Enable CS (LOW)
  HAL_GPIO_WritePin(RAD_1_CS_PORT, RAD_1_CS_PIN, GPIO_PIN_RESET);
  //Transmit and Receive Message
  if(HAL_SPI_TransmitReceive(&hspi1, send_buf, buf, n, HAL_MAX_DELAY) != HAL_OK){
    printf("--[READ] Failed\r\n");
    return E_BGT60UTR13D_COM_ERR;
  }
  //Release CS (HIGH)
  HAL_GPIO_WritePin(RAD_1_CS_PORT, RAD_1_CS_PIN, GPIO_PIN_SET);
  return E_BGT60UTR13D_SUCCESS;
}

bgt60utr13d_err_t write_regs_1(const uint8_t *send_buf, uint32_t n)
{
  //Enable CS (LOW)
  HAL_GPIO_WritePin(RAD_1_CS_PORT, RAD_1_CS_PIN, GPIO_PIN_RESET);
  //Transmit Message
  if(HAL_SPI_Transmit(&hspi1, send_buf, n, HAL_MAX_DELAY) != HAL_OK){
    printf("--[WRITE] Failed\r\n");
    return E_BGT60UTR13D_COM_ERR;
  }
  //Release CS (HIGH)
  HAL_GPIO_WritePin(RAD_1_CS_PORT, RAD_1_CS_PIN, GPIO_PIN_SET);
  return E_BGT60UTR13D_SUCCESS;
}

bgt60utr13d_err_t read_regs_2(const uint8_t *send_buf, uint32_t n, uint8_t *buf)
{
  //Enable CS (LOW)
  HAL_GPIO_WritePin(RAD_2_CS_PORT, RAD_2_CS_PIN, GPIO_PIN_RESET);
  //Transmit and Receive Message
  if(HAL_SPI_TransmitReceive(&hspi2, send_buf, buf, n, HAL_MAX_DELAY) != HAL_OK){
    printf("--[READ] Failed\r\n");
    return E_BGT60UTR13D_COM_ERR;
  }
  //Release CS (HIGH)
  HAL_GPIO_WritePin(RAD_2_CS_PORT, RAD_2_CS_PIN, GPIO_PIN_SET);
  return E_BGT60UTR13D_SUCCESS;
}

bgt60utr13d_err_t write_regs_2(const uint8_t *send_buf, uint32_t n)
{
  //Enable CS (LOW)
  HAL_GPIO_WritePin(RAD_2_CS_PORT, RAD_2_CS_PIN, GPIO_PIN_RESET);
  //Transmit Message
  if(HAL_SPI_Transmit(&hspi2, send_buf, n, HAL_MAX_DELAY) != HAL_OK){
    printf("--[WRITE] Failed\r\n");
    return E_BGT60UTR13D_COM_ERR;
  }
  //Release CS (HIGH)
  HAL_GPIO_WritePin(RAD_2_CS_PORT, RAD_2_CS_PIN, GPIO_PIN_SET);
  return E_BGT60UTR13D_SUCCESS;
}

void drvrlog(char *msg, bool is_err, bool has_int_arg, uint32_t arg)
{
  if(!PRINT_ERRORS_ONLY | is_err)
  {
    if (has_int_arg) {
      printf("%s: %s %#010x\r\n", is_err ? "ERR" : "LOG", msg, arg);
    } else {
      printf("%s: %s\r\n", is_err ? "ERR" : "LOG", msg);
    }
  }
}

/* USER CODE END 0 */

/**
  * @brief  The application entry point.
  * @retval int
  */
int main(void)
{

  /* MCU Configuration--------------------------------------------------------*/

  /* Reset of all peripherals, Initializes the Flash interface and the Systick. */
  HAL_Init();

  /* Configure the system clock */
  SystemClock_Config();

  printf("board booted\n");

  /* Initialize all configured peripherals */
  MX_GPIO_Init();
  MX_SPI1_Init();
  MX_SPI2_Init();
  MX_SPI3_Init();
  MX_SPI6_Init();
  MX_USART1_UART_Init();
  /* USER CODE BEGIN 2 */
  /*CHECK RADAR FOR CONNECTIVITY ______________________________________________________*/
  struct bgt60utr13d_h h_1 = {
      .read_regs = read_regs_1,
      .write_regs = write_regs_1,
      .log = drvrlog,
  };

  struct bgt60utr13d_h h_2 = {
        .read_regs = read_regs_2,
        .write_regs = write_regs_2,
        .log = drvrlog,
    };

  if (bgt60utr13d_init(&h_1) != E_BGT60UTR13D_SUCCESS) {
	  printf("Driver Init failed!\n");
      return -1;
  }

  if (bgt60utr13d_init(&h_2) != E_BGT60UTR13D_SUCCESS) {
  	  printf("Driver Init failed!\n");
        return -1;
    }
  /*CHECK RADAR FOR CONNECTIVITY ______________________________________________________*/

  /*CHECK TOF FOR CONNECTIVITY ______________________________________________________*/
  status = vl53l8cx_is_alive(&Dev, &isAlive);
  if(!isAlive)
  {
	  printf("VL53L8CX with SPI communication not detected, error : %d\n", status);
	  return 255;
  }
  printf("VL53l8cx is alive!\n");

  printf("proceeding to GPIO port check\n");

  for(int i = 0; i < 10; i++) {
	  HAL_GPIO_WritePin(GPIOB, GPIO_PIN_13, GPIO_PIN_SET);
	  HAL_GPIO_WritePin(GPIOB, GPIO_PIN_12, GPIO_PIN_SET);
	  HAL_GPIO_WritePin(GPIOA, GPIO_PIN_3, GPIO_PIN_SET);
	  HAL_GPIO_WritePin(GPIOC, GPIO_PIN_3, GPIO_PIN_SET);
	  HAL_Delay(1000);

	  HAL_GPIO_WritePin(GPIOB, GPIO_PIN_13, GPIO_PIN_RESET);
	  HAL_GPIO_WritePin(GPIOB, GPIO_PIN_12, GPIO_PIN_RESET);
	  HAL_GPIO_WritePin(GPIOA, GPIO_PIN_3, GPIO_PIN_RESET);
	  HAL_GPIO_WritePin(GPIOC, GPIO_PIN_3, GPIO_PIN_RESET);
	  HAL_Delay(1000);
  }
  /*CHECK TOF FOR CONNECTIVITY ______________________________________________________*/
  /* USER CODE END 2 */

  /* Infinite loop */
  /* USER CODE BEGIN WHILE */
  while (1)
  {
    /* USER CODE END WHILE */

    /* USER CODE BEGIN 3 */
  }
  /* USER CODE END 3 */
}

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


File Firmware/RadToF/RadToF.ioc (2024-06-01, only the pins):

Mcu.UserName=STM32H562RIVx
PA0.Signal=GPIO_Output
PA1.Signal=GPIO_Output
PA10.Signal=USART1_RX
PA13(JTMS/SWDIO).Signal=DEBUG_JTMS-SWDIO
PA14(JTCK/SWCLK).Signal=DEBUG_JTCK-SWCLK
PA15(JTDI).Signal=GPIO_Input
PA2.Signal=GPIO_Output
PA3.Signal=GPIO_Output
PA5.Signal=SPI1_SCK
PA6.Signal=SPI1_MISO
PA7.Signal=SPI1_MOSI
PA9.Signal=USART1_TX
PB10.Signal=SPI2_SCK
PB12.Signal=GPIO_Output
PB13.Signal=GPIO_Output
PB14.Signal=GPIO_Input
PB15.Signal=GPIO_Output
PB2.Signal=SPI3_MOSI
PB3(JTDO/TRACESWO).Signal=DEBUG_JTDO-SWO
PB4(NJTRST).Signal=SPI6_MISO
PB5.Signal=SPI6_MOSI
PC1.Signal=SPI2_MOSI
PC10.Signal=SPI3_SCK
PC11.Signal=SPI3_MISO
PC12.Signal=SPI6_SCK
PC13.Signal=GPIO_Output
PC14-OSC32_IN(OSC32_IN).Signal=GPIO_Output
PC15-OSC32_OUT(OSC32_OUT).Signal=GPIO_Output
PC2.Signal=SPI2_MISO
PC3.Signal=GPIO_Output
PC6.Signal=GPIO_Output
PC7.Signal=GPIO_Output
PC8.Signal=GPIO_Output
PD11.Signal=GPIO_Output
PD12.Signal=GPIO_Output

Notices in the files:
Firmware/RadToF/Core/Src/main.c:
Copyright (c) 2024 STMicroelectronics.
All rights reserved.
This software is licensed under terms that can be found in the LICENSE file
